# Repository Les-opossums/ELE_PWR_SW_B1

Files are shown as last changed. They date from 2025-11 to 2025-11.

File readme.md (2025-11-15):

# Power Switch Board - B1
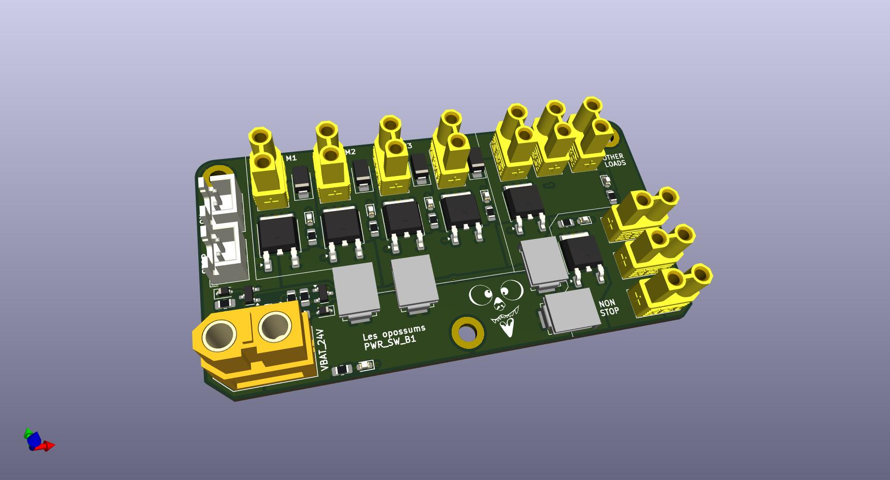
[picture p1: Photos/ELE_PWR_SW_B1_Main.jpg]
main


## Description
This board serves as a power switch for the robot power supplies. It uses the battery as an input (24 V).
Two discrete inputs control the activation of the outputs: emergency stop (STOP) and on/off (ON).

All outputs are commanded by the ON input, while others are also subject to the STOP. The outputs are listed below.
- ON + STOP:
    - Motors 1, 2, 3, and 4.
    - Other loads (3 connectos), reserved for actuators (moving parts of the robot).
- ON only: Non stop loads (3 connectors), reserved for robot logics.

Every output has a corresponding LED for debug. Motors 1 and 2 are connected to one fuse, Motors 3 and 4 to another one. Both other outputs have reserved fuses.

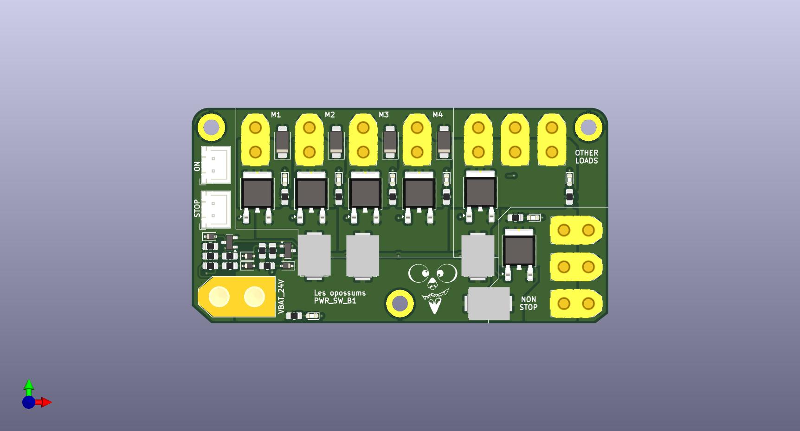
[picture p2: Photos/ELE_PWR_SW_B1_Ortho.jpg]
ortho


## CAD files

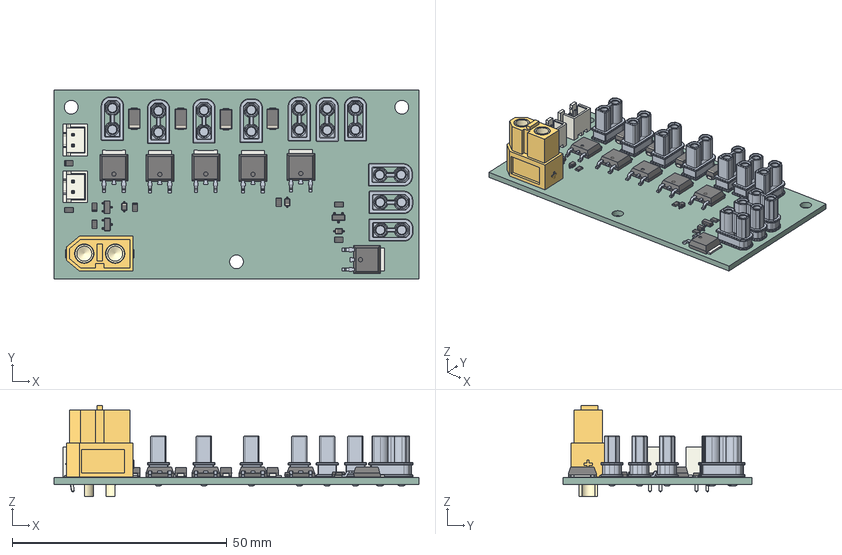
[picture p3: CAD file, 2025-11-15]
ELE_PWR_SW_B1.step
85.0 x 44.0 x 21.2 mm
ASSEMBLY x 10
D_SMA x 4
R_0805_2012Metric x 8
SOT_23 x 3
CQ assembly x 6
D_SOD_323 x 3
XT60 female v5
JST_B2B_XH_A x 2
power_hub_PCB

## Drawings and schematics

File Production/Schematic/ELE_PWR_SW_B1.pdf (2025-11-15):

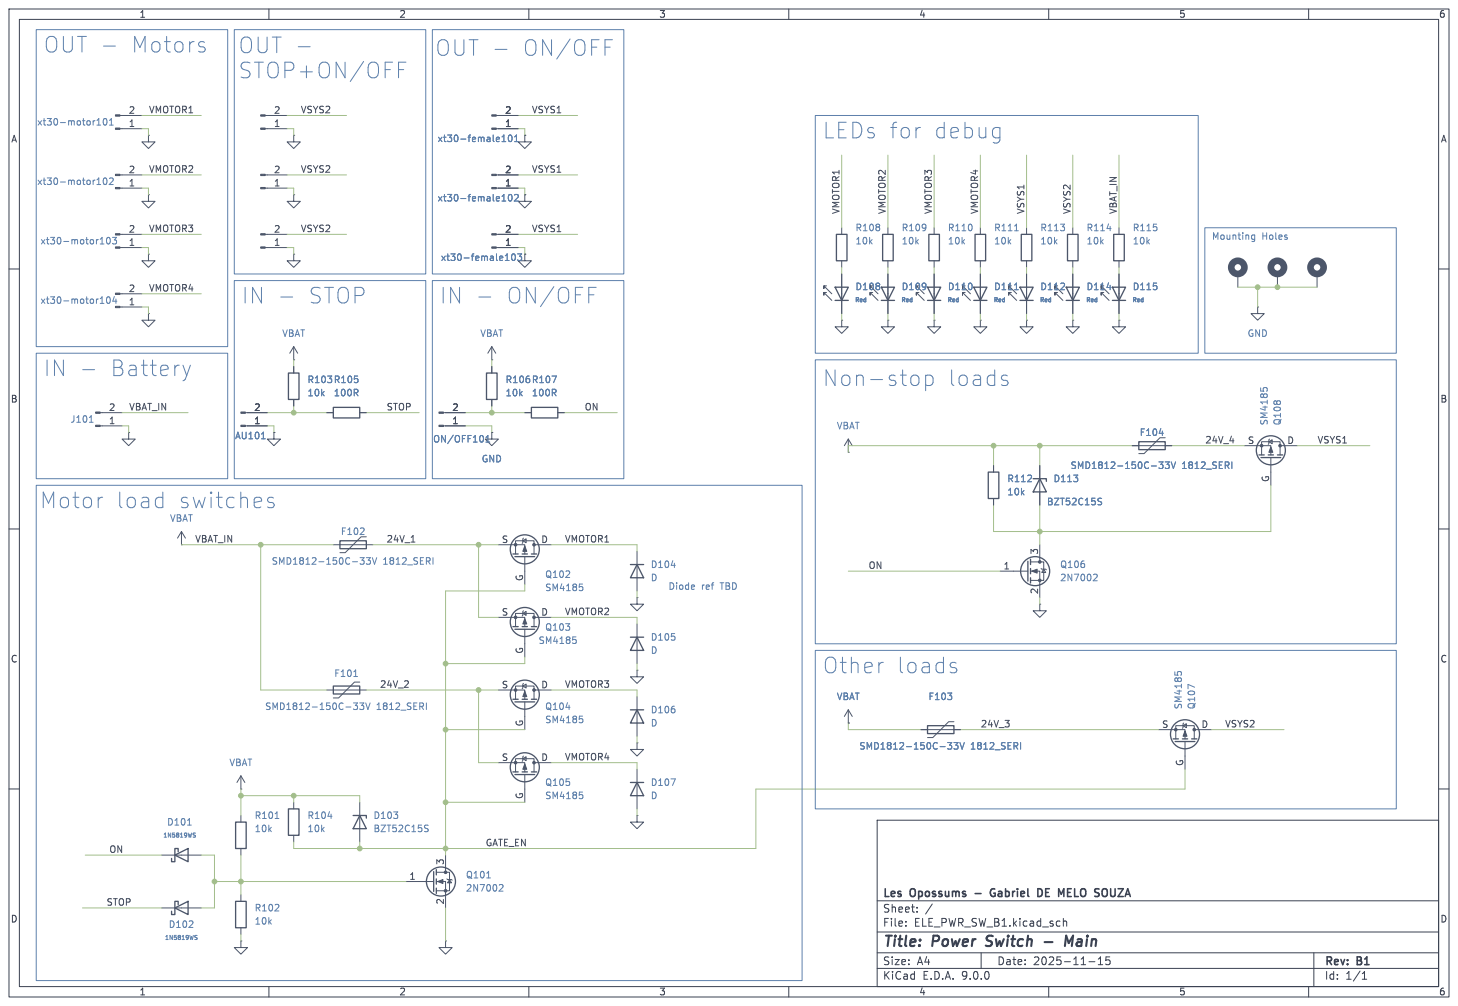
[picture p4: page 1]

OUT - STOP+ON/OFF

Mounting Holes Other loads

Id: 1/1 Title: Power Switch - Main

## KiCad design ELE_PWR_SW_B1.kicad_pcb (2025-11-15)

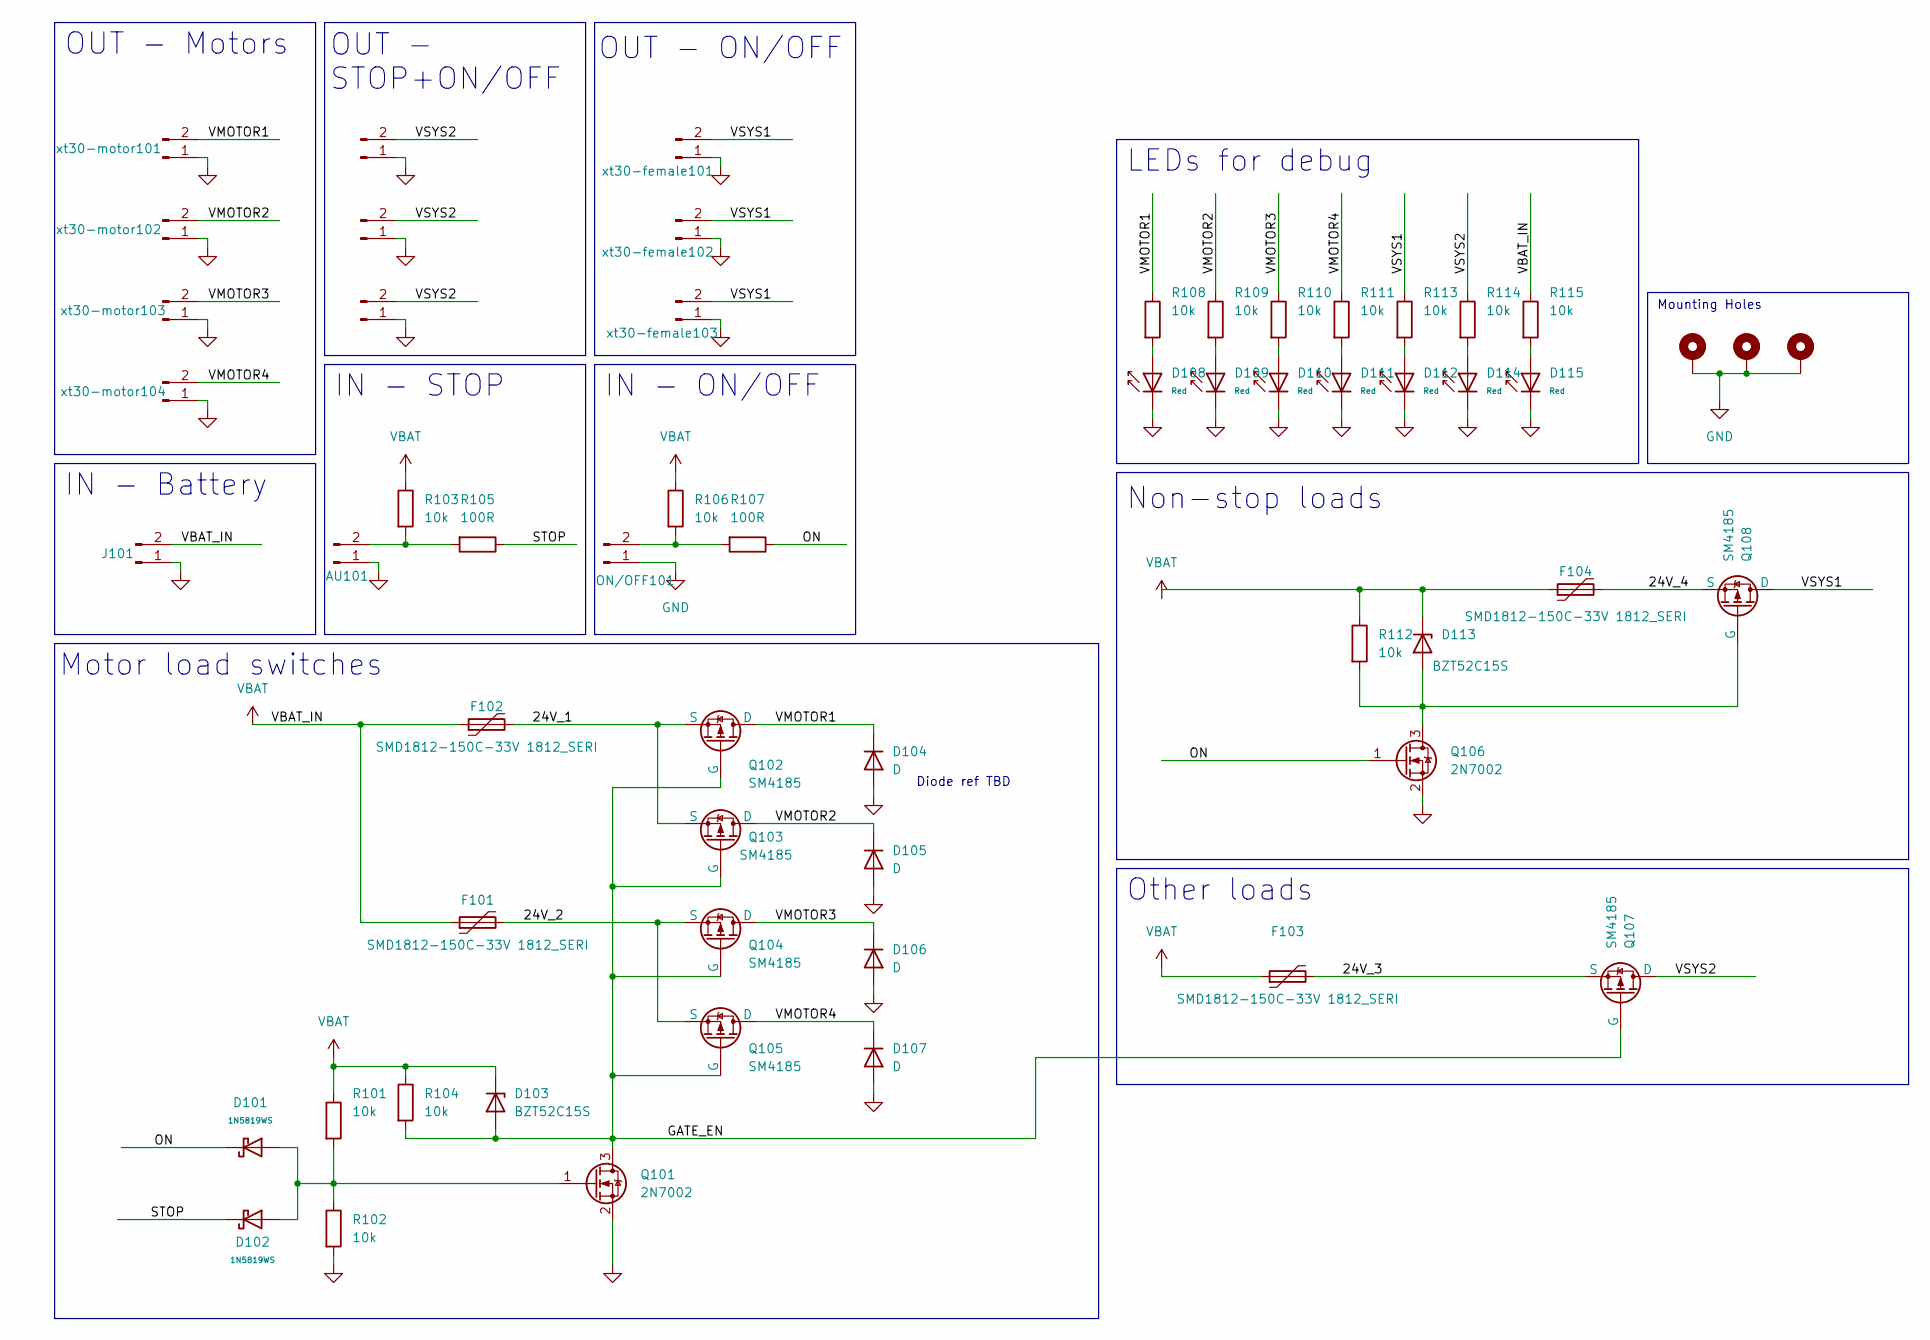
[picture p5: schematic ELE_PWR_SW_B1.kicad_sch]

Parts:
AU101: Conn_01x02_Pin; JST_XH_B2B-XH-AM_1x02_P2.50mm_Vertical
D101, D102: 1N5819WS; D_SOD-323; Forward Voltage (Vf@If) 600mV@1A; Reverse Voltage (Vr) 40V; Part 1N5819WS; LCSC C191023
D103, D113: BZT52C15S; D_SOD-323
D104, D105, D106, D107: D; D_SMA
D108, D109, D110, D111, D112, D114, D115: Red; D_0603; Part KT-0603R; LCSC C2286
F101, F102, F103, F104: SMD1812-150C-33V 1812_SERI; Fuse_Bourns_MF-SM_7.98x5.44mm
H101, H102, H103: MountingHole_Pad; MountingHole_3.2mm_M3_DIN965_Pad
J101: Conn_01x02_Pin; AMASS_XT60-M_1x02_P7.20mm_Vertical
ON/OFF101: Conn_01x02_Pin; JST_XH_B2B-XH-AM_1x02_P2.50mm_Vertical
Q101, Q106: 2N7002; SOT-23
Q102, Q103, Q104, Q105, Q107, Q108: SM4185; TO-252-2
R101, R102, R103, R104, R106, R108, R109, R110, R111, R112, R113, R114, R115: 10k; R_0805_2012Metric_Pad1.20x1.40mm_HandSolder
R105, R107: 100R; R_0805_2012Metric_Pad1.20x1.40mm_HandSolder
xt30-female101, xt30-female102, xt30-female103, xt30-motor101, xt30-motor102, xt30-motor103, xt30-motor104, xt30-motor105, xt30-motor106, xt30-motor107: Conn_01x02_Pin; AMASS_XT30U-F_1x02_P5.0mm_Vertical

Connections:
/24V_1: F102.2, Q102.3 (S), Q103.3 (S)
/24V_2: F101.2, Q104.3 (S), Q105.3 (S)
/24V_3: F103.2, Q107.3 (S)
/24V_4: F104.2, Q108.3 (S)
/GATE_EN: D103.2 (A), Q101.3 (D), Q102.1 (G), Q103.1 (G), Q104.1 (G), Q105.1 (G), Q107.1 (G), R104.2
/ON: D101.1, Q106.1 (G), R107.1
/STOP: D102.1, R105.1
/VMOTOR1: D104.1 (K), Q102.2 (D), R108.1, xt30-motor101.2
/VMOTOR2: D105.1 (K), Q103.2 (D), R109.1, xt30-motor102.2
/VMOTOR3: D106.1 (K), Q104.2 (D), R110.1, xt30-motor103.2
/VMOTOR4: D107.1 (K), Q105.2 (D), R111.1, xt30-motor104.2
/VSYS1: Q108.2 (D), R113.1, xt30-female101.2, xt30-female102.2, xt30-female103.2
/VSYS2: Q107.2 (D), R114.1, xt30-motor105.2, xt30-motor106.2, xt30-motor107.2
GND: AU101.1, D104.2 (A), D105.2 (A), D106.2 (A), D107.2 (A), D108.1, D109.1, D110.1, D111.1, D112.1, D114.1, D115.1, H101.1, H102.1, H103.1, J101.1, ON/OFF101.1, Q101.2 (S), Q106.2 (S), R102.2, xt30-female101.1, xt30-female102.1, xt30-female103.1, xt30-motor101.1, xt30-motor102.1, xt30-motor103.1, xt30-motor104.1, xt30-motor105.1, xt30-motor106.1, xt30-motor107.1
unnamed: AU101.2, R103.2, R105.2
unnamed: D108.2, R108.2
unnamed: D109.2, R109.2
unnamed: D110.2, R110.2
unnamed: D111.2, R111.2
unnamed: D112.2, R113.2
unnamed: D113.2 (A), Q106.3 (D), Q108.1 (G), R112.2
unnamed: D114.2, R114.2
unnamed: D115.2, R115.2
unnamed: ON/OFF101.2, R106.2, R107.2
unnamed: D101.2, D102.2, Q101.1 (G), R101.2, R102.1
VBAT: D103.1 (K), D113.1 (K), F101.1, F102.1, F103.1, F104.1, J101.2, R101.1, R103.1, R104.1, R106.1, R112.1, R115.1

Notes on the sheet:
OUT - STOP+ON/OFF
OUT - Motors
OUT - ON/OFF
IN - STOP
Motor load switches
IN - Battery
LEDs for debug
Mounting Holes
Diode ref TBD
Other loads
IN - ON/OFF
Non-stop loads

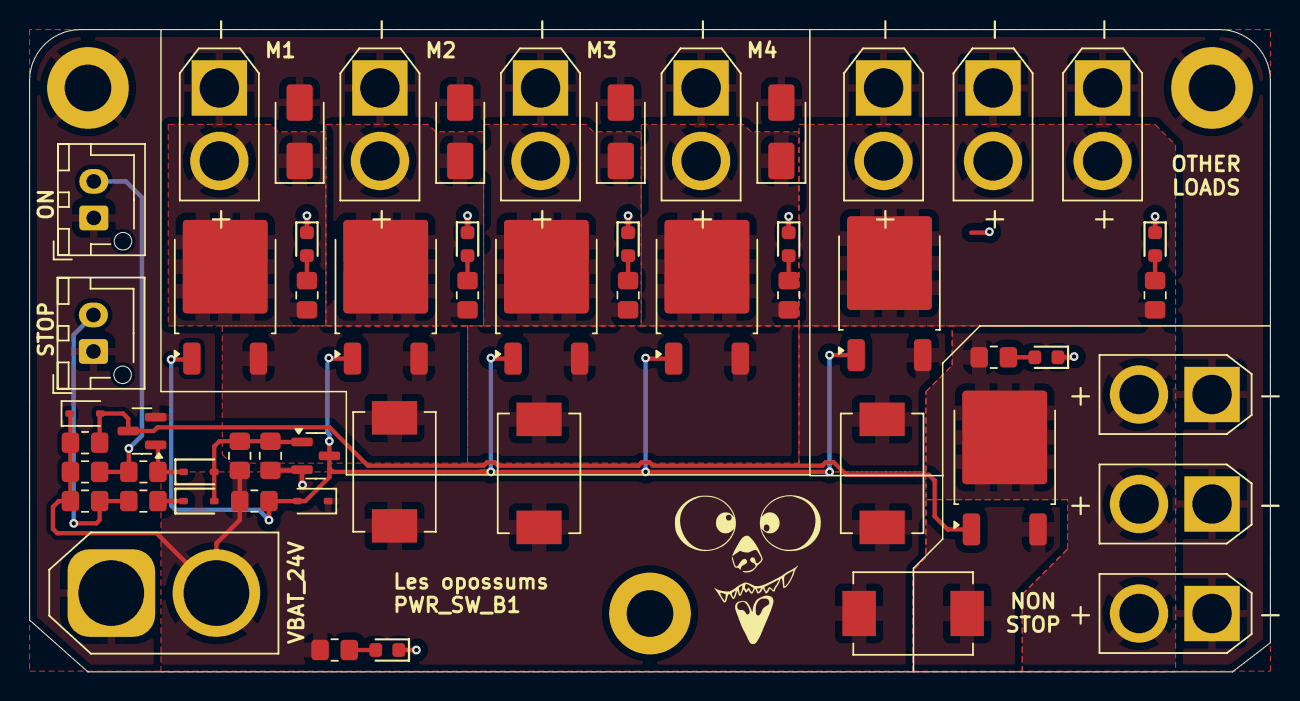
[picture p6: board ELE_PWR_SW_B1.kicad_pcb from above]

Board: 2 copper layers, 85.0 x 44.0 mm, 58 parts (0 on the bottom side), 26 nets.
